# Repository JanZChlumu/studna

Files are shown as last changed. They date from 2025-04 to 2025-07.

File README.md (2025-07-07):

# Projekt Studna
> Se skládá ze 2 nezávislých částí
> - Ochrana domácí vodárny
> - Měření výšky hladiny

## Ochrana domácí vodárny
Do studny je umístěn [hladinový spínač](./img/Instalace_2.png), který sepne při kriticky nízké hladině. Tím se odpojí (3 fázová) domácí vodárna, aby se systém nezavzdušnil a čerpadlo neshořelo. [Schema v rozvaděči](./HW/Silnoproud_ochrana_cerpadla/darling_ochrana.pdf)

## Měření výšky hladiny
Motivace:
- Do studny byl při rekonstrukci zaveden UTP kabel. 
- Pramen není příliš silný v letních měsících je třeba šetřit vodou.

Snaha byla o levné řešení, hlavně na straně senzoru, které v případě nefunkčnosti bude možné snadno upgradovat na "profi drahé" řešení.
Levné řešení (cena 10USD) je ultrazvukový modul více níže.
Drahé řešení je např. [hydrostatický snímač TSH-37](https://www.fiedler.company/sites/default/files/dokumenty/datasheet_tsh37.pdf) jeho cena (v roce 2025) je cca 8.000Kč.

Pro obě řešení zůstane stejná komunikace mezi senzorem a řídící jednotkou a to přes RS485. TSH-37 vyžaduje protokol Modbus RTU na což není SW momentálně připraven.

### Základní blokové schema:

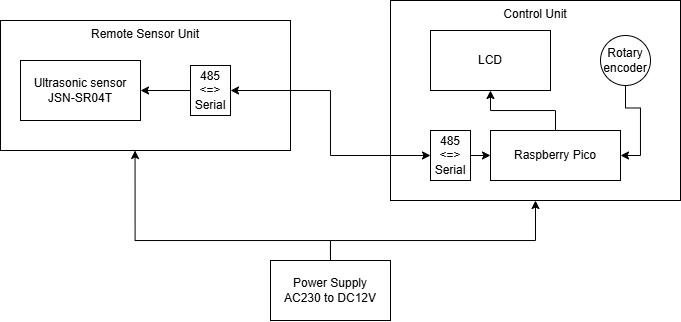
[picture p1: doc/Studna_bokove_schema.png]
BlokoveSchema


- [Schema řídící jednotky](./HW/kicad/lcd/lcd.pdf)
- Schema Remote Sensor Unit neexistuje -  je poměrně triviální.

### Ultrazvukové čidlo
Waterproof Ultrasonic Module JSN-SR04T
[zajímavostí o modulu (schema a módy)](https://forum.mysensors.org/topic/11417/jsn-sr04t-distance-sensor-reliability-issue-fix/6)

**Limity a omezení**, __které možná ovlivní vaše rozhodnutí o jeho nepoužití__.
- Měřený rozsah je přibližně od 25cm do 230cm.
- Přesnost je **kvantována v krocích 1,7cm**.

Tyto limity se nedají v softwaru řídící jednotky nijak kompenzovat, jsou dány konstrukcí modulu JSN-SR04T.

Možné příčiny limitů:
- **"Kvantování"**: zvuk se ve vzduchu šíří přibližně rychlostí 343 m/s. Když se podíváme, jak daleko zvuk urazí za 1 mikrosekundu:

$$
d = v \cdot t = 343 \text{m/s} \cdot 1 \mu s = 0{,}000 343 \text{m} = 0{,}0343 \text{cm}
$$

Jelikož vzdálenost se měří tam i zpět, a nás zajímá jen cesta tam, **čas se dělíme dvěma**,a to znamená, že rozlišení senzoru závisí na **časovém rozlišení** měření:

Např. pokud vnitřní časovač v modulu meří s přesností 100µs, pak bude kvantovací krok:

$$
0{,}0343 \text{cm} \cdot 100 \mu \cdot \frac{1}{2} \approx 1{,}7 \text{cm}
$$

Myslím, že modul JSN-SR04T vyhodnocuje či vzorkuje echo s frekvencí cca 10kHz, tedy žádná sláva a **odtud plyne nepřesnost**.

- Ve vzdálenosti < než 25cm se nestačí odražené echo detekovat.
- Ve vzdálenosti > než cca 230cm či vyšší vnitřní čítač přeteče a modul vrátí maximální hodnotu. Pokud se žádné echo nevrátí (detektor míří do volného prostoru) maximální hodnota bývá v intervalu (230,250) cm. S jistou rezervou je měření validní **do 220 cm**.

#### Použitý mód JSN-SR04T
se měmí hodnotou rezistoru viz datasheet; Mode 3: Mode=120K (or short M2 bit directly) UART controlled output
The UART controlled output method outputs the measured distance value (hexadecimal number)
according to the UART communication format. In this method, the trigger command 0X55 signal
needs to be added to the RX pin. The module measures once every time the command is received. The foot outputs the measured
distance value. The command trigger cycle should be greater than 60ms

# SW
Snaha byla použít co nejjednodušší a kýmkoli lehce upravitelé řešení.

- Vývojové prostředí je Thonny
- Zdrojové kódy jsou v MicroPythonu.
	- Vše co je třeba do Raspberry Pico nahrát je ve složce ./SW/2Pico/ 
	- [Konfigurační soubor](./SW/2Pico/config.json) a provozní data jsou uložena v json souborech v file systému, protože Raspberry Pico nemá vlastní EEPROMku. Limit je max. 100tis přepsání, což je zcela dostatečné, protože json soubory se ukládaní jen sporadicky.
	- Použité knihovny (složka ./SW/2Pico/lib/ , jsou lehce upravené (projekty pod MIT licencemi), změny nejsou nikde zdokumentovány.
- Tvorba vlastních fontů pro LCD je popsána [zde](./SW/tools/fonts/README.md)

# TODOs & BUGs

- HW
	- PCB Control unit layout:
		- opravit všechna poudra tranzistorů; Momentálně se dá deska osadit, ale všechny tranzistory se musí debilně otočit o 120stupňů.
		- posunout kondenzátor C7; usnadní se montáž
	- [Navrhnout PCB pro Remote sensor Unit](./img/Instalace_1.png); aby to nevypadalo takto...
	- přidat STL model krabičky
- SW
	- Dopnit do Menu možnost konfigurovat průměr studny pro výpočet litrů.
	- Bug: shadow vs stored data - v podmenu Historie grafů se přepisuje nově změněná hodnota. Fix: v menu nespouštět měřící task.

# Finální produkt
Trochu fotodokumentace [více zde](./img/)
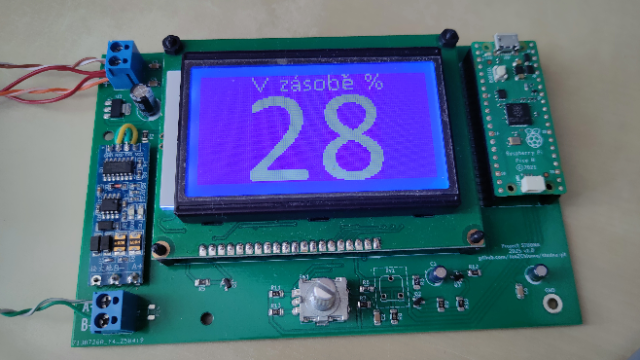
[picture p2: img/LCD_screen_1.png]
PCB

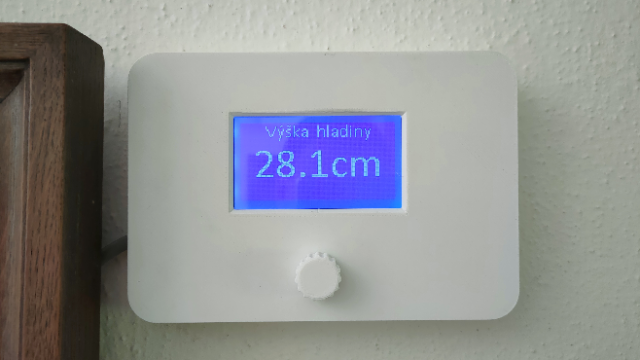
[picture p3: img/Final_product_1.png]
NaZdi1

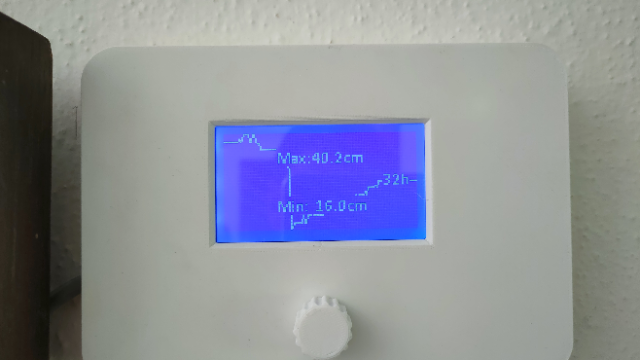
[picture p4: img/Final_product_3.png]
NaZDi2

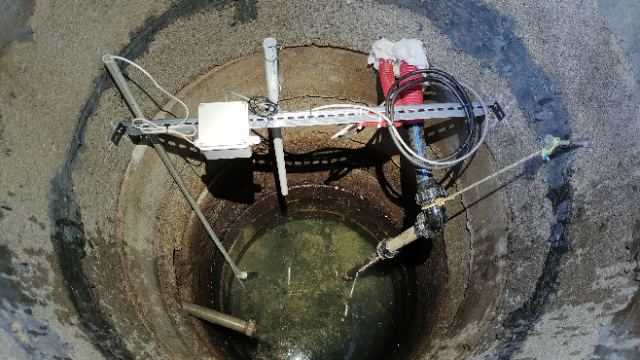
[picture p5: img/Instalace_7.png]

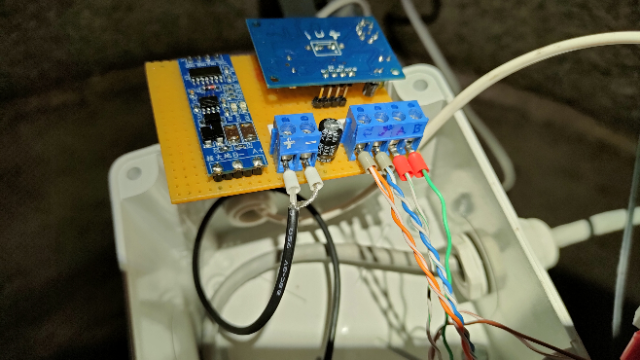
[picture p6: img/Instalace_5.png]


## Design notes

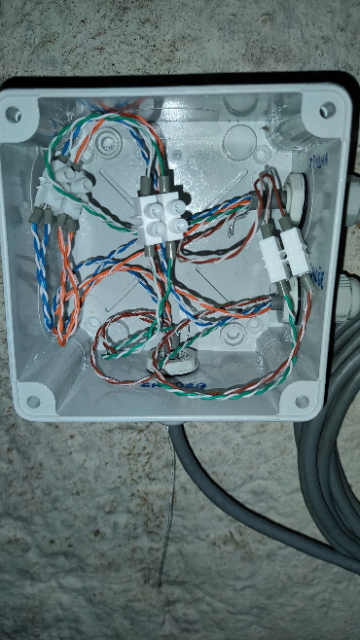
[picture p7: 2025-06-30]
img/Instalace_9.png

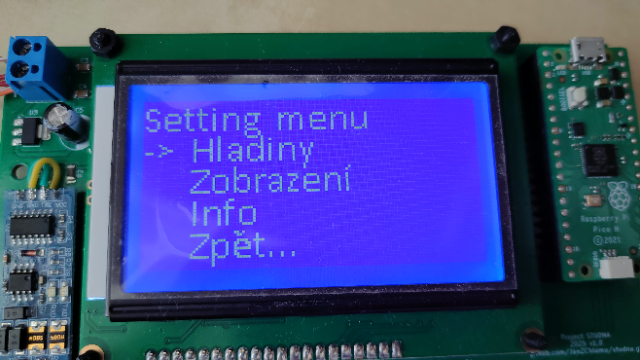
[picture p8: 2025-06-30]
img/LCD_screen_2.png

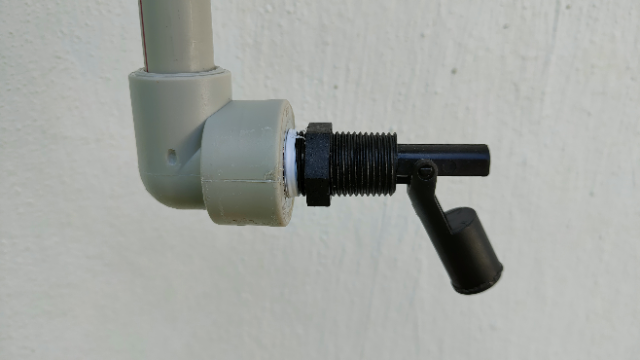
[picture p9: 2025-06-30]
img/Instalace_2.png

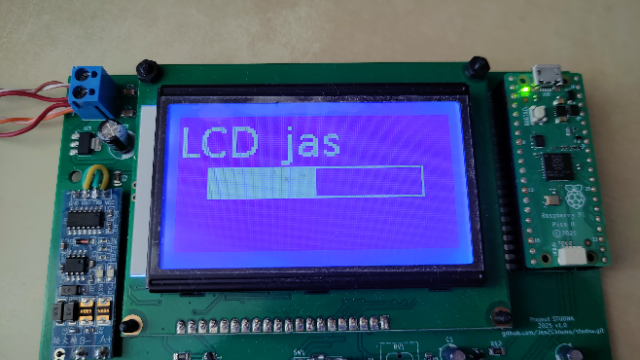
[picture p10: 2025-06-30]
img/LCD_screen_3.png

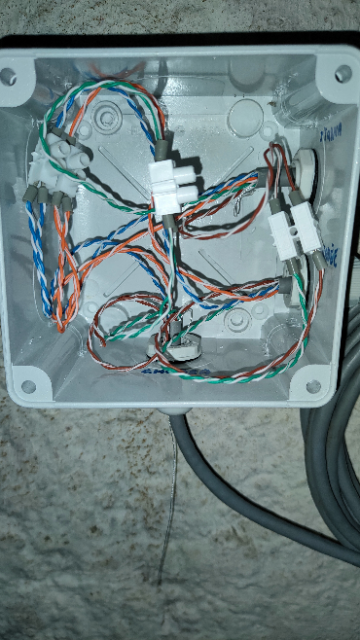
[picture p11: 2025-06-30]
img/Instalace_8.png

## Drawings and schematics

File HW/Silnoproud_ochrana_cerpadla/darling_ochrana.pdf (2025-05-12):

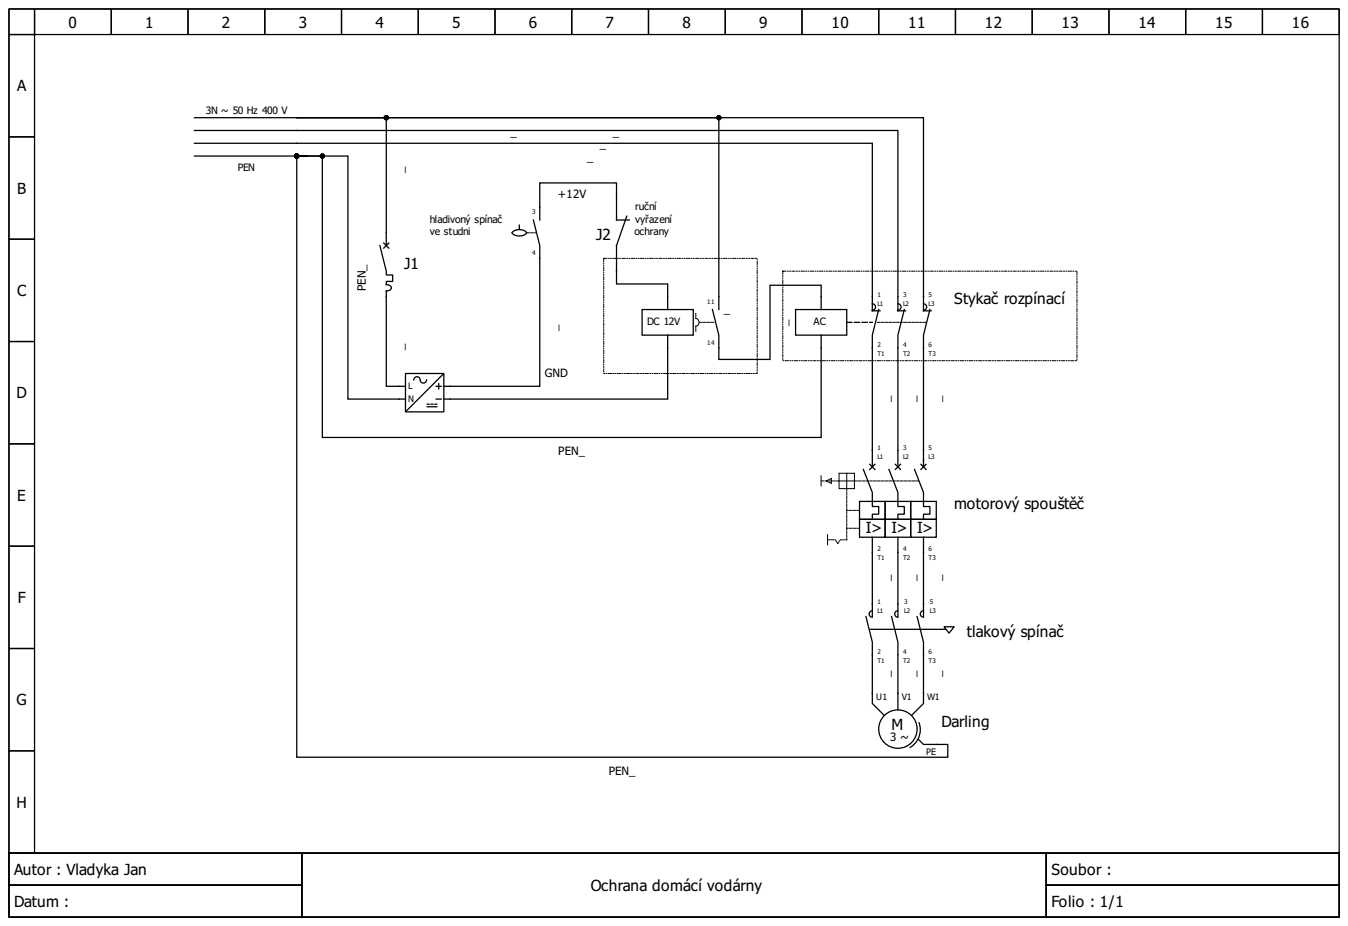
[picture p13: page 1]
Soubor :; Datum :; Folio : 1/1; PEN; ruční vyřazení ochrany J2; hladivoný spínač ve studni; motorový spouštěč; Stykač rozpínací; Darling; tlakový spínač; PEN_; GND

Autor : Vladyka Jan

Ochrana domácí vodárny

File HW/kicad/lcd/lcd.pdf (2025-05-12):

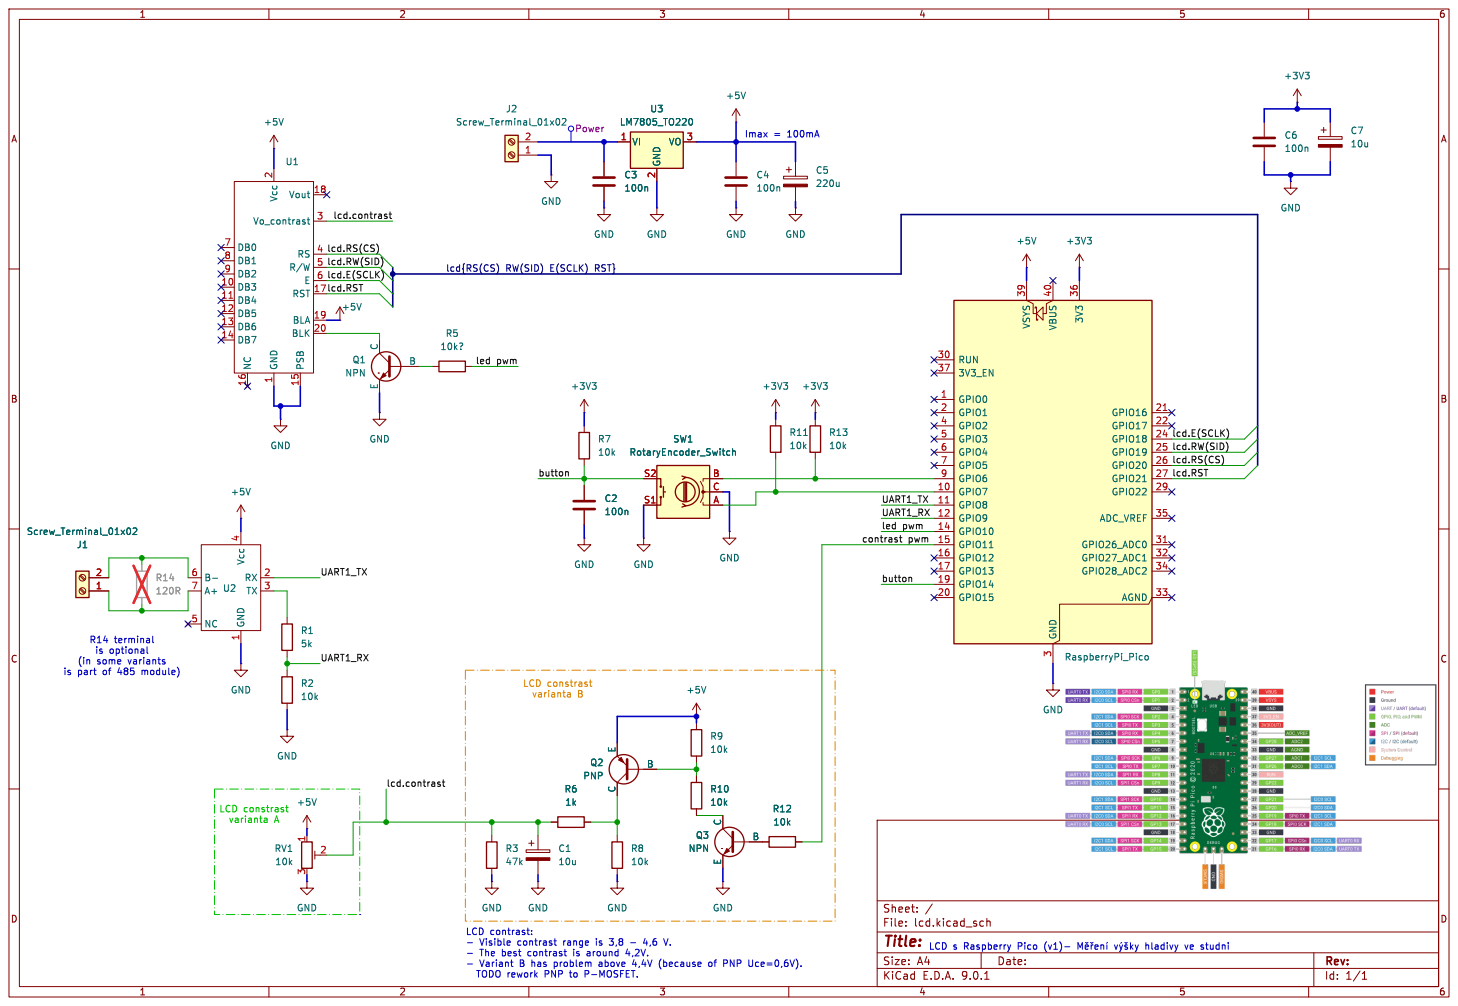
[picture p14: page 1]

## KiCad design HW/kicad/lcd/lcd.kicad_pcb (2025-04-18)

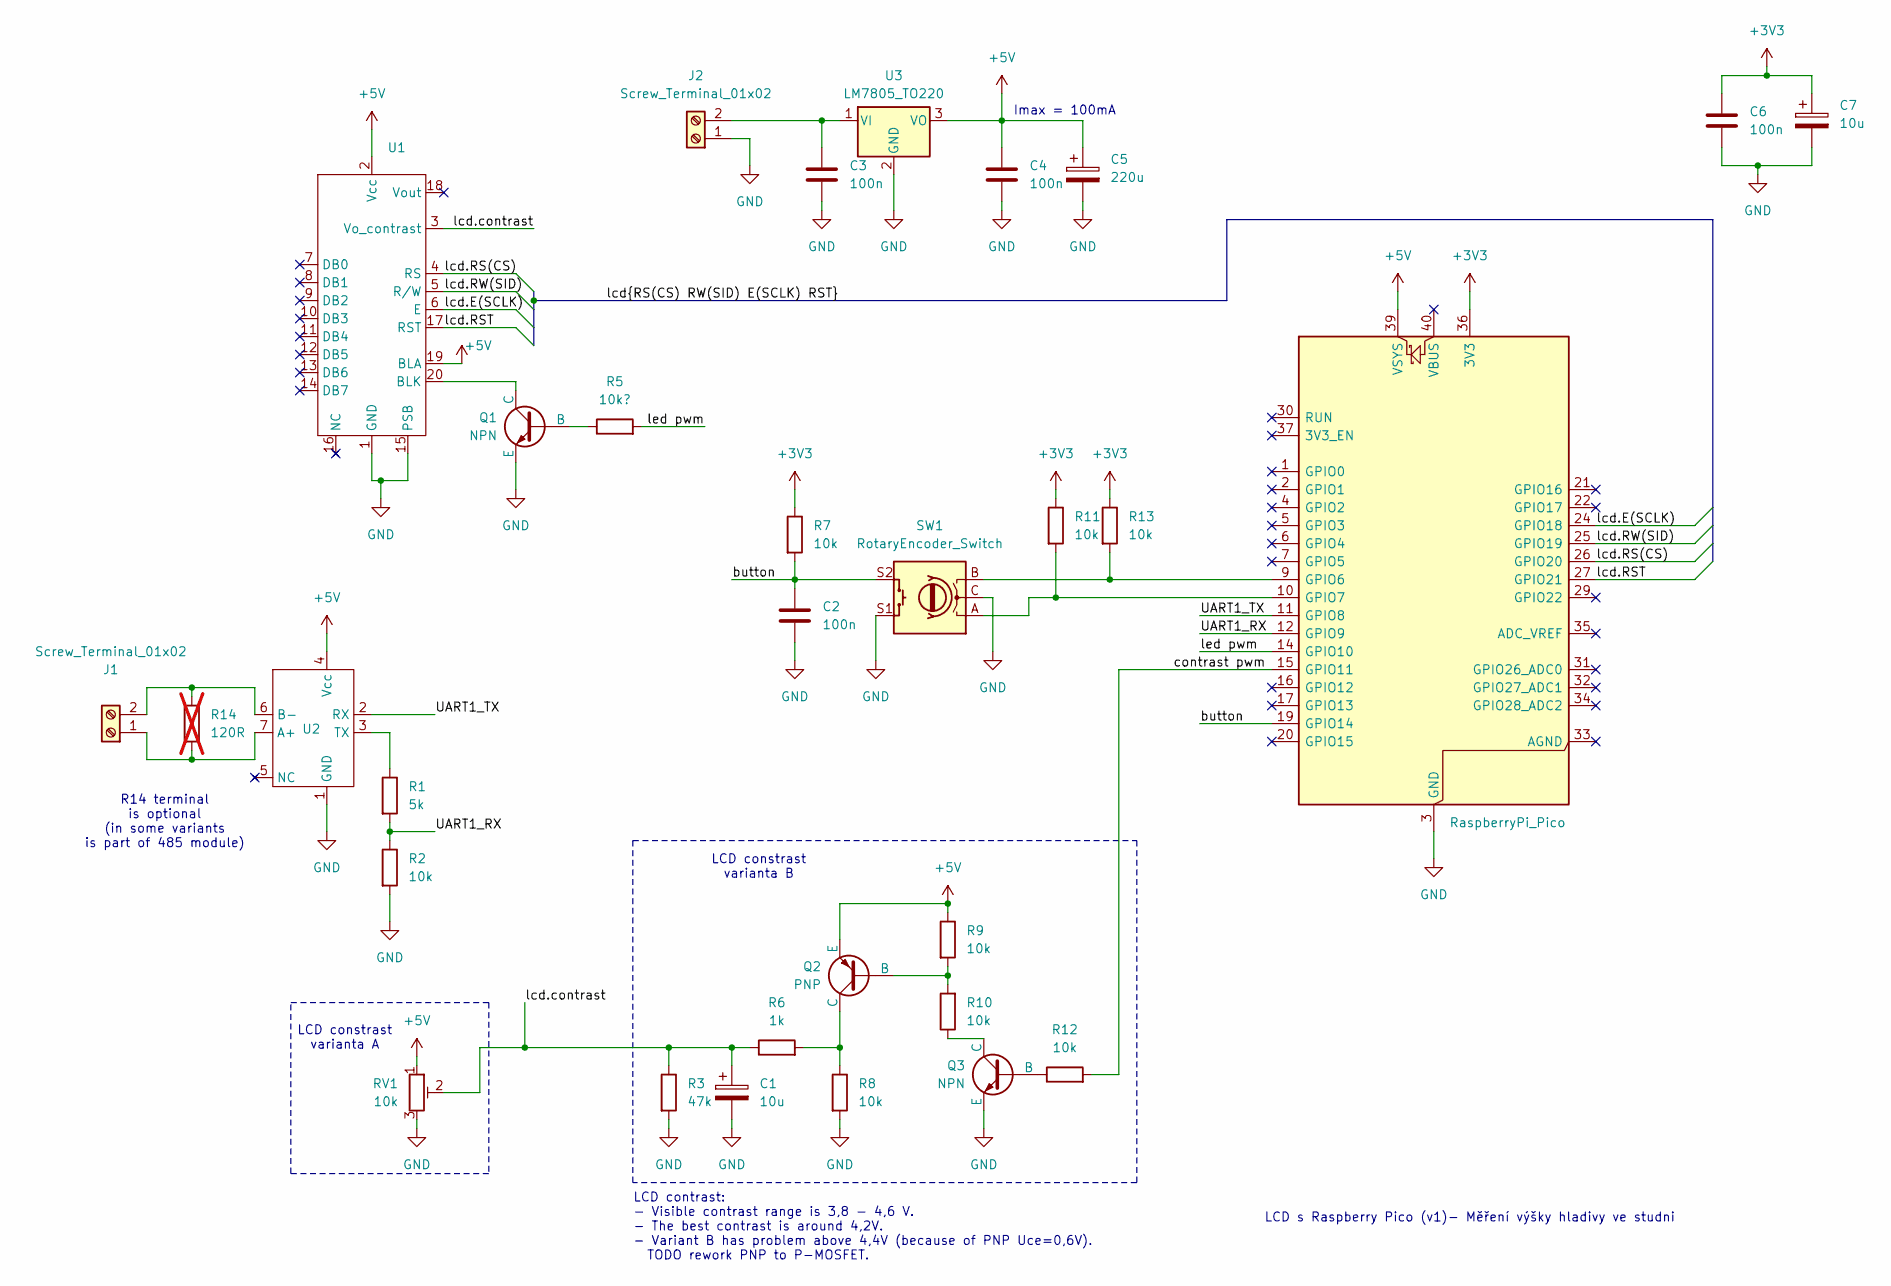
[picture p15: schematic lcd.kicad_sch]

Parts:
A1: RaspberryPi_Pico; RaspberryPi_Pico_Common_NO_wifi
C1, C7: 10u; CP_Radial_D5.0mm_P2.00mm
C2, C3, C4, C6: 100n; C_1206_3216Metric
C5: 220u; CP_Radial_D8.0mm_P2.50mm
J1, J2: Screw_Terminal_01x02; TerminalBlock_MaiXu_MX126-5.0-02P_1x02_P5.00mm
Q1, Q3: NPN; SOT-23
Q2: PNP; SOT-23
R1: 5k; R_1206_3216Metric
R2, R7, R8, R9, R10, R11, R12, R13: 10k; R_1206_3216Metric
R3: 47k; R_1206_3216Metric
R5: 10k?; R_1206_3216Metric
R6: 1k; R_1206_3216Metric
R14: 120R; R_1206_3216Metric; not fitted
RV1: 10k; Potentiometer_Runtron_RM-065_Vertical
SW1: RotaryEncoder_Switch; RotaryEncoder_Alps_EC11E-Switch_Vertical_H20mm
U1: LCD 128x64
U2: 485 modul
U3: LM7805_TO220; SOT-223-3_TabPin2

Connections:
+3V3: A1.36 (3V3), C6.1, C7.1, R7.1, R11.1, R13.1
+5V: A1.39 (VSYS), C4.1, C5.1, Q2.3 (E), R9.1, RV1.1, U1.2 (Vcc), U1.19 (BLA), U2.4 (Vcc), U3.3 (VO)
/UART1_RX: A1.12 (GPIO9), R1.2, R2.1
/UART1_TX: A1.11 (GPIO8), U2.2 (RX)
/button: A1.19 (GPIO14), C2.1, R7.2, SW1.S2
/contrast pwm: A1.15 (GPIO11), R12.2
/lcd.E(SCLK): A1.24 (GPIO18), U1.6 (E)
/lcd.RS(CS): A1.26 (GPIO20), U1.4 (RS)
/lcd.RST: A1.27 (GPIO21), U1.17 (RST)
/lcd.RW(SID): A1.25 (GPIO19), U1.5 (R/W)
/lcd.contrast: C1.1, R3.1, R6.1, RV1.2, U1.3 (Vo_contrast)
/led pwm: A1.14 (GPIO10), R5.2
GND: A1.3 (GND), A1.8 (GND), A1.13 (GND), A1.18 (GND), A1.23 (GND), A1.28 (GND), A1.38 (GND), C1.2, C2.2, C3.2, C4.2, C5.2, C6.2, C7.2, J2.1, Q1.3 (E), Q3.3 (E), R2.2, R3.2, R8.2, RV1.3, SW1.C, SW1.S1, U1.1 (GND), U1.15 (PSB), U2.1 (GND), U3.2 (GND); also elsewhere on the board
unnamed: A1.9 (GPIO6), R13.2, SW1.B
unnamed: A1.10 (GPIO7), R11.2, SW1.A
unnamed: J1.1, R14.2, U2.7 (A+)
unnamed: J1.2, R14.1, U2.6 (B-)
unnamed: C3.1, J2.2, U3.1 (VI)
unnamed: Q1.2 (B), R5.1
unnamed: Q1.1 (C), U1.20 (BLK)
unnamed: Q2.2 (B), R9.2, R10.2
unnamed: Q2.1 (C), R6.2, R8.1
unnamed: Q3.2 (B), R12.1
unnamed: Q3.1 (C), R10.1
unnamed: R1.1, U2.3 (TX)

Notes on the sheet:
LCD constrast varianta A
LCD s Raspberry Pico (v1)- Měření výšky hladivy ve studni
LCD constrast varianta B
LCD contrast: - Visible contrast range is 3,8 - 4,6 V. - The best contrast is around 4,2V. - Variant B has problem above 4,4V (because of PNP Uce=0,6V). TODO rework PNP to P-MOSFET.
R14 terminal is optional (in some variants is part of 485 module)
Imax = 100mA

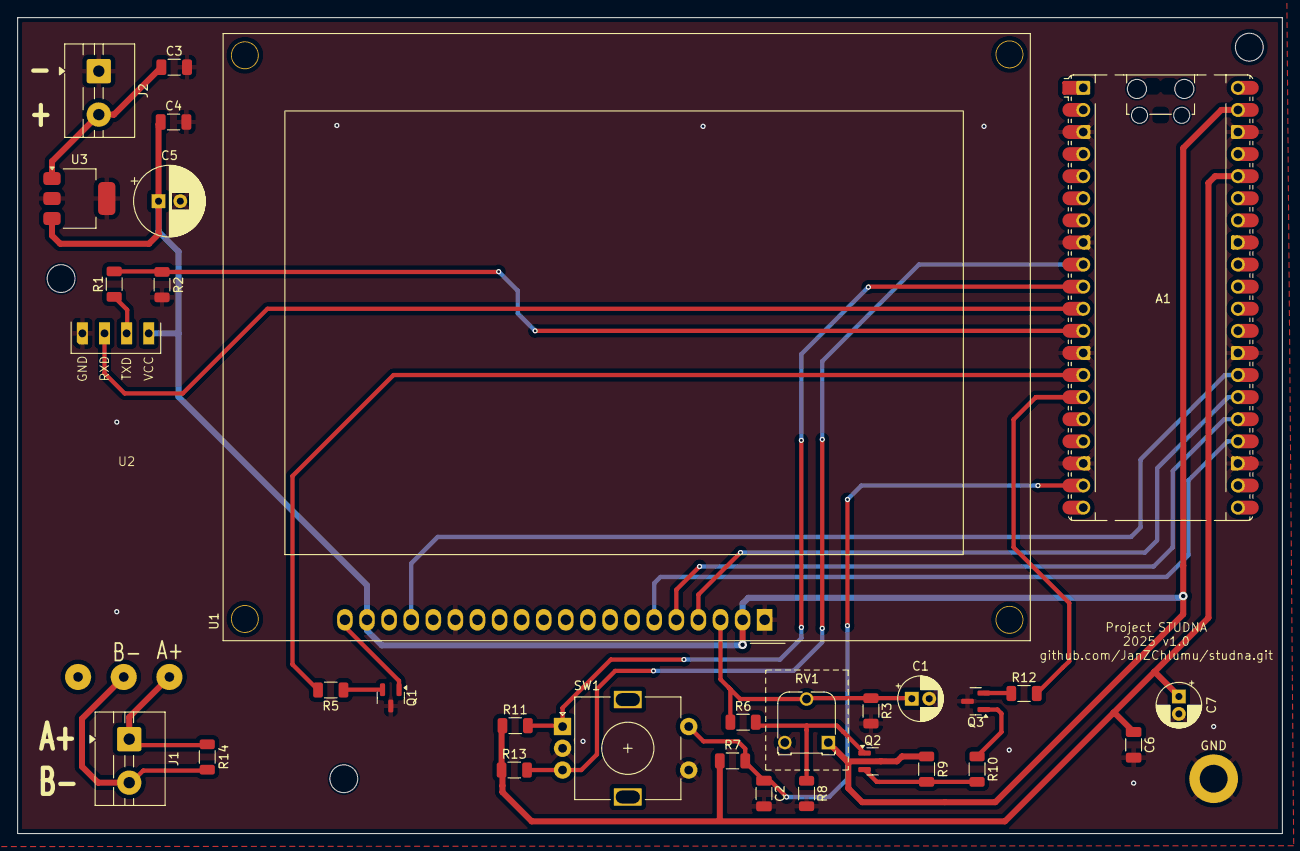
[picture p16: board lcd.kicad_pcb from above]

Board: 2 copper layers, 145.4 x 93.8 mm, 32 parts (0 on the bottom side), 25 nets.

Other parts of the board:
GND: MountingHole_3.2mm_M3_DIN965_Pad

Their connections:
GND: GND.1; also elsewhere on the board

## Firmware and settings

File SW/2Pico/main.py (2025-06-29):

from machine import Pin, SPI, Timer, PWM, UART
from utime import sleep
import time
import ujson  # JSON pro ukládání strukturovaných dat
import uos
from rotary_irq_rp2 import RotaryIRQ
import lcd12864_spi
from lcd12864_spi import LCD12864_SPI
import Calibri10CZ  as F10_FONT
import Calibri12CZ  as F12_FONT
import Calibri16CZ as F16_FONT
import Calibri24CZ as F24_FONT
import Calibri36CZ as F36_FONT
import Calibri80CZ as F80_FONT

semaphore = 1  # Binární semafor (1 = volný, 0 = obsazený)

def acquire_semaphore():
    """Pokud je semafor volný (1), nastavíme ho na obsazený (0) a vrátíme True."""
    global semaphore
    if semaphore == 1:
        semaphore = 0
        return True
    return False

def release_semaphore():
    """Uvolní semafor (nastaví na 1)."""
    global semaphore
    semaphore = 1

FILE_CONFIG = "config.json"
FILE_HISTORY = "hist_data.json"

# Definice viceurovnoveho menu
menu = {
    "Nastavení":    ["Hladiny"      , "Zobrazení"       , "Info"            , "Zpět..."],
    "Hladiny":      ["Min"          , "Max"             , "H reference" , "Zpět..."],
    "Zobrazení":    ["Graf historie", "LCD jas"         , "LCD kontrast"    , "Zpět..."],
    "Info":         ["Hist. maxima" , "RESET Historie"  , "Průměruj vzorky" , "Zpět..."]
}
# testovací konfigurace pro emulovanou EEPROM
test_config_data = {"Min":             {"val": 20, "rotmax": 200, "rotstep" : 1, "unit": "cm"},
                    "Max":             {"val": 40, "rotmax": 200, "rotstep" : 1, "unit": "cm"},
                    "H reference": {"val": 0, "rotmax": 250, "rotstep" : 1, "unit": "cm", "rotmin" : 0},
                    "Graf historie":   {"val": 0, "rotmax": 2, "rotstep" : 1, "unit": "hodin"},
                    "LCD jas":         {"val": 2, "rotmax": 30, "rotstep" : 1},
                    "LCD kontrast":    {"val": 4, "rotmax": 30, "rotstep" : 2},
                    "RESET Historie":  {"val": 0, "rotmax": 3, "rotstep" : 1},
                    "Průměruj vzorky":   {"val": 1, "rotmax": 7, "rotstep" : 1, "rotmin" : 1, "unit" : "vzorky"}} 

do_action = None # jméno probíhající akce
selected_text = "" # na tento text ukazuje šipka v menu "->"
action_tmp_file__rmax = None  # dočasná hodnota z konfiguračního souboru, vyžadují některé akce
action_tmp_file__unit = None  # dočasná hodnota z konfiguračního souboru, vyžadují některé akce

graph_data = {"8h": [], "16h": [], "32h": [], "counter": 0}
home_screens_show_data = {"dist_cm": -1, "percent": -1, "liters": -1 ,"error": 0}

current_menu = "Nastavení"
selected_action = 0

# Seznam položek menu
home_screens_list = ["Home_%", "Home_cm", "Home_graf", "Home_liters"]
ActualHomeScreen = home_screens_list[3] 

hist_data_shadow = {"min": 0, "max": 0}

def save_file(file_name, data):
    try:
        with open(file_name, "w") as f:
            ujson.dump(data, f)
            print("File saved")
    except OSError:
        print("Error saving config")        

def load_file(file_name):
    try:
        with open(file_name, "r") as f:
            print(f"File loaded {file_name}")
            return ujson.load(f)
    except OSError:
        print("File not found")
        return None  # Soubor neexistuje

#print("!!!!!!! test confguration !!!!!!!!!")
#save_file(FILE_CONFIG, test_config_data)    #TOdo remove later

file_ram_shadow_data = {}

def load_cfg_to_shadow_ram(file_data):
    global file_ram_shadow_data
    print("load_cfg_for_home_screens")
    if file_ram_shadow_data is None:
        file_ram_shadow_data = {"Min": 0, "Max": 0, "GraphHrs": 0, "ReferenceShift": 0}
    if file_data is not None:
        try:
            file_ram_shadow_data["Min"] = file_data["Min"]["val"]
            file_ram_shadow_data["Max"] = file_data["Max"]["val"]
            file_ram_shadow_data["GraphHrs"] = file_data["Graf historie"]["val"]
            file_ram_shadow_data["ReferenceShift"] = file_data["H reference"]["val"]
            file_ram_shadow_data["AvgNo"] = file_data["Průměruj vzorky"]["val"]
            file_ram_shadow_data["LCD jas"] = file_data["LCD jas"]["val"]
            file_ram_shadow_data["LCD jas max"] = file_data["LCD jas"]["rotmax"]            
            file_ram_shadow_data["LCD kontrast"] = file_data["LCD kontrast"]["val"]
            file_ram_shadow_data["LCD kontrast max"] = file_data["LCD kontrast"]["rotmax"]
        except OSError:
            print("load_cfg_for_home_screens | no key found")
 
load_cfg_to_shadow_ram(load_file(FILE_CONFIG))

def load_history_info(file_data):
    global hist_data_shadow    
    print("load_history_info")
    if hist_data_shadow is None:
        hist_data_shadow = {"min": 0, "max": 0}
    if file_data is None:
        # Pokud soubor neexistuje, vytvoř nový
        file_data = {"min_vody": 0, "max_vody": 0}
        save_file(FILE_HISTORY, file_data)
        hist_data_shadow["min"] = 0
        hist_data_shadow["max"] = 0
    else:
        try:
            hist_data_shadow["min"] = file_data["min_vody"]
            hist_data_shadow["max"] = file_data["max_vody"]
        except OSError:
            print("load_history_info | no key found")
    
load_history_info(load_file(FILE_HISTORY)) #INIT

def save_history_info():
    global hist_data_shadow
    if hist_data_shadow is not None:
        _file_data = load_file(FILE_HISTORY)
        if _file_data is None:
            # Pokud soubor neexistuje, vytvoř nový
            _file_data = {"min_vody" : hist_data_shadow["min"], "max_vody" : hist_data_shadow["max"]}
        else:
            _file_data["min_vody"] = hist_data_shadow["min"]
            _file_data["max_vody"] = hist_data_shadow["max"]
        save_file(FILE_HISTORY, _file_data)
        print("History saved")
    
def update_history_data(distance):
    global hist_data_shadow
    if distance is not None:
        _update = False
        if hist_data_shadow["min"] == 0 or distance < hist_data_shadow["min"]:
            hist_data_shadow["min"] = distance
            _update = True
        if hist_data_shadow["max"] == 0 or distance > hist_data_shadow["max"]:
            hist_data_shadow["max"] = distance
            _update = True        
        if _update:
            save_history_info()
            print(f"History updated min {hist_data_shadow['min']} max {hist_data_shadow['max']}")

# Inicializace UART1 pro Raspberry Pi Pico 
uart1 = UART(1, baudrate=9600, tx=Pin(8), rx=Pin(9))  # Nastav piny dle zapojení

distances = []
max_records = 128  # Počet měření za posledních 6 hodin -> uložit každé 12 měření á 15 sec.

pwmLCD = PWM(Pin(10))
pwmLCD.freq(1000) # PWM 1kHz

pwmContrast = PWM(Pin(11))
pwmContrast.freq(1000) # PWM 1kHz
MIN_PWM_CONTRAST = 0
MAX_PWM_CONTRAST = 65535

spi = SPI( 0, baudrate = 1_000_000, polarity = 1, phase = 1 )
lcd = LCD12864_SPI( spi = spi, cs_pin = 20, rst_pin = 21, rotation = 0 )
lcd.clear()
UpdateLCD = False

# Inicializace rotačního enkodéru
rot = RotaryIRQ(pin_num_clk=6, pin_num_dt=7, min_val=0, max_val=5, reverse=True, range_mode=RotaryIRQ.RANGE_WRAP, pull_up=True)

# Inicializace tlačítka potvrzení
button = Pin(14, Pin.IN, Pin.PULL_UP)
button_debounce_time_ms = 21
button_debounce_timer = Timer(-1) # -1 means SW timer 

led = Pin("LED", Pin.OUT)

def rotary_menu_reset_and_set_to_max(value):
    global RotaryPlausibleVal
    rot.reset() # = set(value = 0) #toto neni vhodne pro Akce
    rot.set(max_val = value, incr = 1, min_val = 0)
    RotaryPlausibleVal = value #zabrání překreslení LCD
    #toto pridej global selected_action = 0
    print(f"Rotary reset & set to max {rot.get_max_val()}")    

rotary_menu_reset_and_set_to_max(len(home_screens_list) - 1)

def map_value(x, in_min, in_max, out_min, out_max):
    mapped_value = (x - in_min) * (out_max - out_min) / (in_max - in_min) + out_min
    print(f"map_value -> {x} | {in_min} {in_max} | {out_min} {out_max} | -> {mapped_value}")
    return int(mapped_value)    

def measure_ultrasonic():
    if not acquire_semaphore():  
        return None  # Pokud je semafor obsazený, měření neproběhne

    uart1.write(b'\x55')  # Odeslání příkazu pro měření
    time.sleep(0.05)  # Krátká pauza (2 ms)

    distance = None
    if uart1.any() >= 4:
        start_byte = uart1.read(1)
        if start_byte == b'\xff':
            data = uart1.read(3)
            if data and len(data) == 3:
                h_data, l_data, checksum = data
                result = (h_data << 8) + l_data
                if ((255 + h_data + l_data) & 0xFF) == checksum:
                    distance = result
                else:
                    print("Invalid result")                    
    print(f"measure_ultrasonic {distance}")    
    release_semaphore()  # Uvolnění semaforu po dokončení
    return distance

def get_distance():    
    global home_screens_show_data, file_ram_shadow_data    
    _refShift_mm = file_ram_shadow_data["ReferenceShift"] * 10 #convert mm to cm    
    # average samples    
    if file_ram_shadow_data.get("AvgNo", 1) > 1:                
        distances = []
        for i in range(file_ram_shadow_data["AvgNo"]):
            dist_mm = measure_ultrasonic()
            if dist_mm is not None:
                dist_mm = _refShift_mm - dist_mm
                if dist_mm < 0:                                        
                    home_screens_show_data["error"] = -1
                else:                    
                    distances.append(dist_mm)                        
        if len(distances) > 0:
            avg = sum(distances) / len(distances)
            print(f"get_distance_AVG | dist_mm {distances} | avg {avg}")
            return avg
    else:
        # no average samples        
        dist_mm = measure_ultrasonic()
        if dist_mm is not None:
            dist_mm = _refShift_mm - dist_mm
            if dist_mm < 0:                
                home_screens_show_data["error"] = -1                
            print(f"get_distance | dist_mm {dist_mm}")
    return dist_mm

def draw_error_msg():
    global home_screens_show_data
    if home_screens_show_data["error"] != 0:        
        lcd.set_font(F12_FONT)
        lcd.draw_text("Uprav ref. hladinu", 0, 50, center_x=True, clear_background=True) # x axis is centered
        home_screens_show_data["error"] = 0
    
def draw_home_graph_hrs():
    global UpdateLCD
    if UpdateLCD:
        lcd.fill(0)    
        map_hours = {0: "8h", 1: "16h", 2: "32h"}
        _hr = file_ram_shadow_data["GraphHrs"]
        if _hr in map_hours: 
            distances = graph_data[map_hours[_hr]]

            if len(distances) > 0:                
                min_distance = min(distances)
                max_distance = max(distances)                                
                range_distance = max_distance - min_distance                                                
                # Prevent division by zero if all distances are the same
                if range_distance == 0:
                    scale = 63
                else:
                    scale = 63 / range_distance

                for i in range(1, len(distances)):
                    x1 = int((i - 1) * 128 / max_records)
                    y1 = 63 - int((distances[i - 1] - min_distance) * scale)
                    x2 = int(i * 128 / max_records)
                    y2 = 63 - int((distances[i] - min_distance) * scale)
                    lcd.line(x1, y1, x2, y2, 1)
                # write over graph
                lcd.set_font(F12_FONT)
                lcd.draw_text("Max:" + str(max_distance/10) + "cm", 5, 10, center_x=True, clear_background=True)
                lcd.draw_text( map_hours[_hr] , 105, 25, clear_background=True)    
                lcd.draw_text("Min: " + str(min_distance/10) + "cm", 5, 42, center_x=True, clear_background=True)
            else:
                lcd.text("Nejsou data pro ", 5, 20, 1)
                lcd.text( " " + map_hours[_hr] + " graf ", 25, 30, 1)
        else:
            print("Invalid key in map_hours")                    
        draw_error_msg()
        lcd.show()
        UpdateLCD = False

"""
HAPTIC Timer call cyclic
"""
def haptic(timer):    
    global RotaryPlausibleVal, UpdateLCD, ActualHomeScreen    
    _val = rot.value()
    if RotaryPlausibleVal != _val:
        RotaryPlausibleVal = _val
        UpdateLCD = True
        print(f"Rotary value {RotaryPlausibleVal} | max {rot.get_max_val()}")
        if ActualHomeScreen is not None:
            ActualHomeScreen = home_screens_list[RotaryPlausibleVal]

hapticTimer = Timer(-1)
hapticTimer.init(period=19, mode=Timer.PERIODIC, callback=haptic) 

#cyclicaly update data for all homescreens
def task1(timer):    
    global UpdateLCD, home_screens_show_data    
    _dist_cm = ""
    _percent = ""
    _liters  = ""
    _hole_diameter_cm = 100 #prumer studny v cm
    led.toggle()
    dist_mm = get_distance()
    if dist_mm is not None:                    
        update_history_data(dist_mm) #update history data        
        if ActualHomeScreen in home_screens_list:
            _dist_cm = round(float(dist_mm / 10), 1)
            _percent = int((((dist_mm/10) - file_ram_shadow_data["Min"]) * 100)/file_ram_shadow_data["Max"])
            _liters = int((((3.14*_hole_diameter_cm*_hole_diameter_cm)/4)*(_dist_cm - file_ram_shadow_data["Min"]))/1000)
            print(f"task1 | dist_cm {_dist_cm} | percent {_percent} | liters {_liters} | actual_home_screen {ActualHomeScreen}")            
    else:
        _dist_cm = "?"
        _percent = "?"
        _liters  = "?"
    home_screens_show_data.update({"dist_cm": _dist_cm, "percent": _percent, "liters": _liters})
    UpdateLCD = True    

tim = Timer(-1)
tim.init(period=5*1000, mode=Timer.PERIODIC, callback=task1)

# called by Timer (timStoreGraph) in basic period for 8hours graph
def updateGraphData(_):
    global graph_data
    print("updateGraphData")
    _arrray_max = 128
    _dist = get_distance()    
    if _dist is not None:
        #8h store
        graph_data["8h"].append(_dist)
        if len(graph_data["8h"]) > _arrray_max:
            graph_data["8h"].pop(0)
        print("updateGraphData | data 8h", graph_data["8h"]) #TODO tohle ukaze cely list!
        # 16h store
        if graph_data["counter"] % 2 == 0:
            graph_data["16h"].append(_dist)
            if len(graph_data["16h"]) > _arrray_max:    
                graph_data["16h"].pop(0)
            print("updateGraphData | data 16h", graph_data["16h"])
        # 32h store
        if graph_data["counter"] % 4 == 0:
            graph_data["32h"].append(_dist)
            if len(graph_data["32h"]) > _arrray_max:    
                graph_data["32h"].pop(0)
            print("updateGraphData | data 32h", graph_data["32h"])
    graph_data["counter"] += 1 # for storage modulo

"""
Historie pro grafy se ukládá jen v ram. LCD má rozlišení 128x64 pixelů, takže max 128 bodů uložíme pro každý graf.
Pro 8h graf uložíme hodnotu každých 225 sec, pro 16h graf každých 450 sec a pro 32h graf každých 900 sec.
"""
timStoreGraph = Timer(-1)
timStoreGraph.init(period=1000*225, mode=Timer.PERIODIC, callback=updateGraphData)
#timStoreGraph.init(period=2500, mode=Timer.PERIODIC, callback=updateGraphData) # testing short time

def draw_action_set_value(desc, value, unit = None):
    """ Draw a value on the display
    Args:
    desc (str): Description of the value
    value (int): Value to be displayed
    """
    global UpdateLCD
    if UpdateLCD:
        lcd.fill(0)
        lcd.set_font(F16_FONT)
        lcd.set_text_wrap()
        if unit is not None:
            text = str(value) + unit
        else:
            text = str(value)
        lcd.draw_text(desc, 0, 0)
        lcd.set_font(F36_FONT)
        lcd.draw_text(text, 5, 20, center_x=True)
        lcd.show()
        UpdateLCD = False

def draw_action_reset_history(desc, value):
    _map = {0 : "Ne", 1 : "Možná?", 2 : "Ano", 3 : "Možná?"}
    draw_action_set_value(desc, _map[value])

def draw_action_graph_time_base(desc, value, unit = None):
    try:
        map_hours = {0: 8, 1: 16, 2: 32}
    except KeyError:
        value = 0  # Default value if key is not found        
        print("Invalid key in map_hours")
    draw_action_set_value(desc, map_hours[value], unit)

def draw_action_bar(text_desc, fill_percentage):
    """ Draw a horizontal bar with adjustable fill
    Args:
    fill_percentage (int): Fill level from 0 to 100
    """
    global UpdateLCD
    if UpdateLCD:        
        print(fill_percentage)
        #lcd.fill(0)
        lcd.set_font(F24_FONT)
        lcd.set_text_wrap()        
        lcd.draw_text(text_desc, 0, 0)        
        bar_width = 100
        bar_height = 15
        x_start = 14
        y_start = 25
        filled_width = int((fill_percentage / 100) * bar_width)    
        # Draw bar border
        lcd.rect(x_start, y_start, bar_width, bar_height, 1)    
        # clear - rewrite by white color
        lcd.fill_rect(x_start+1, y_start+1, bar_width-2, bar_height-2, 0)    
        # Draw filled portion
        lcd.fill_rect(x_start, y_start, filled_width, bar_height, 1)    
        lcd.show()
        UpdateLCD = False


def draw_testingFonts():
    global UpdateLCD
    if UpdateLCD:
        lcd.fill(0)
        lcd.set_font(F16_FONT)
        lcd.set_text_wrap()        
        lcd.draw_text("Historická data %ěščřžýá∑∞", 0, 0)
        lcd.show()                        
        UpdateLCD = False        

def draw_action_info_history_extrems():
    global UpdateLCD    
    if UpdateLCD:
        lcd.fill(0)
        lcd.set_font(F16_FONT)
        lcd.set_text_wrap()
        lcd.draw_text("Historické extrémy", 0, 0)        
        lcd.draw_text("Min : " + str(hist_data_shadow["min"]/1000) + " m", 0, 20)
        lcd.draw_text("Max : " + str(hist_data_shadow["max"]/1000) + " m", 0, 30)
        lcd.draw_text("Ø z " + str(file_ram_shadow_data["AvgNo"]) + " vzorků", 0, 50)
        lcd.show()                        
        UpdateLCD = False
        print("draw_history_maximums")

def draw_home_screen_cm():
    global UpdateLCD, home_screens_show_data
    if UpdateLCD:
        lcd.fill(0)        
        lcd.set_font(F16_FONT)        
        lcd.draw_text("Výška hladiny", 0, 0, center_x=True)
        lcd.set_font(F36_FONT)        
        lcd.draw_text(str(home_screens_show_data["dist_cm"]) + "cm", 0, 15, center_x=True)                                
        draw_error_msg()
        lcd.show()                        
        UpdateLCD = False

def draw_home_screen_liters():
    global UpdateLCD, home_screens_show_data
    if UpdateLCD:
        lcd.fill(0)        
        lcd.set_font(F16_FONT)        
        lcd.draw_text("Litrů v zásobě", 5, -2, center_x=True)
        lcd.set_font(F80_FONT)        
        lcd.draw_text(str(home_screens_show_data["liters"]), 0, -2, center_x=True)        
        draw_error_msg()
        lcd.show()
        UpdateLCD = False


def draw_home_screen_percent():
    global UpdateLCD, home_screens_show_data
    if UpdateLCD:
        lcd.fill(0)        
        lcd.set_font(F16_FONT)        
        lcd.draw_text("V zásobě %", 5, -2, center_x=True)
        lcd.set_font(F80_FONT)        
        lcd.draw_text(str(home_screens_show_data["percent"]), 0, -2, center_x=True)        
        draw_error_msg()
        lcd.show()
        UpdateLCD = False


pwmLCD.duty_u16(map_value(file_ram_shadow_data["LCD jas"], 0, file_ram_shadow_data["LCD jas max"], 0, 65535)) # 0-100%
pwmContrast.duty_u16(map_value(file_ram_shadow_data["LCD kontrast"], 0, file_ram_shadow_data["LCD kontrast max"], MIN_PWM_CONTRAST, MAX_PWM_CONTRAST)) # 0-100%

def draw_menu():        
    global UpdateLCD
    #print("draw_menu")
    """ Vykresli aktualni menu na LCD """
    lcd.fill(0)
    lcd.set_font(F16_FONT)
    lcd.draw_text(current_menu, 0, 0)

    for i, item in enumerate(menu[current_menu]):
        prefix = "-> " if i == selected_action else "   "
        lcd.draw_text(prefix + item, 0, 12 + i * 12)

    lcd.show()
    UpdateLCD = False

def navigate_menu():
    """ Posune kurzor nahoru nebo dolu v menu """
    global selected_action
    if UpdateLCD:
        print("navigate_menu")
        selected_action = RotaryPlausibleVal
        draw_menu()

def entry_action(action):
    global do_action, action_tmp_file__unit, action_tmp_file__rmax, RotaryPlausibleVal, UpdateLCD
    
    # načti z konfiguračního souboru
    cfg = load_file(FILE_CONFIG)
    if cfg is None:
        print("Error loading config")
        do_action = None
        rotary_menu_reset_and_set_to_max(len(menu[current_menu]) - 1) #reset to menu
    else:
        lcd.clear()
        UpdateLCD = True        
        try:
            if action in cfg:
                action_tmp_file__rmax = cfg[action]["rotmax"]
                _val = cfg[action]["val"]
                _step = cfg[action]["rotstep"]

                RotaryPlausibleVal = _val
                rot.set(value = _val, max_val = action_tmp_file__rmax, incr = _step)
                print(f"entry action {action} | file load: val {_val}, rmax {action_tmp_file__rmax}, step {_step}.")
                
                # non standard keys...
                if "unit" in cfg[action]:
                    action_tmp_file__unit = cfg[action]["unit"]
                else:
                    action_tmp_file__unit = None
                if "rotmin" in cfg[action]:
                    rot.set(min_val = cfg[action]["rotmin"])
        except OSError:
            print("Klic neni nenalezen") # pouzij defaultni hodnoty z menu
            action_tmp_file__rmax = len(menu[current_menu]) - 1        
            rotary_menu_reset_and_set_to_max(action_tmp_file__rmax)            
        
        do_action = action
        print(f"Entry action {action}. Rotary max {rot.get_max_val()}")
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

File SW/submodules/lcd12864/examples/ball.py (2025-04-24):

from machine import Pin, SPI
from lcd12864_spi import LCD12864_SPI
from time import sleep_ms

spi = SPI( 1, baudrate = 1_000_000, polarity = 1, phase = 1 )
lcd = LCD12864_SPI( spi = spi, cs_pin = 15, rst_pin = 4, rotation = 1 )

lcd.fill(0)

radius = 4

x_border = lcd.width - 1
y_border = lcd.height - 1

prev_x = radius
prev_y = radius

x = radius
y = radius

x_speed = 2
y_speed = 2

while True:    
    lcd.ellipse(prev_x, prev_y, radius, radius, 0, True) # clear previos
    lcd.ellipse(x, y, radius, radius, 1, True)
    prev_x = x
    prev_y = y
    
    x += x_speed
    y += y_speed
    
    if x + radius > x_border or x - radius < 0:
        x_speed = -x_speed
        
    if y + radius > y_border or y - radius < 0:
        y_speed = -y_speed    
    
    lcd.show() 


    

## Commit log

2025-03-27 timers changes to SW
2025-04-10 lcd pin change
2025-04-13 update LCD pwm range
2025-04-14 Kicad LCD pcb
    [lcd.kicad_pcb, lcd.kicad_sch]
2025-04-15 change mounting holes
    [lcd.kicad_pcb]
2025-04-18 pcb ramecek potenciometru
    [lcd.kicad_pcb]
2025-04-24 re-order project structure
    [lcd-B_Cu.gbr, lcd-B_Mask.gbr, lcd-B_Paste.gbr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]
2025-05-16 fix Copilot fuckup :/
    [main.py]
2025-05-30 fix H-referece problems, change grahic info, update README
    [main.py]
